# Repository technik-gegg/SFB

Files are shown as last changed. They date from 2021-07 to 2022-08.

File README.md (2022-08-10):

# Welcome to the SFB project

This is the firmware for the **S**mart **F**ilament **B**uffer as published on [Printables](https://www.printables.com/de/model/197621-smart-filament-buffer-2) and [Thangs](https://thangs.com/mythangs/file/58718).

The Smart Filament Buffer (used for multi-material 3D printing) comes with an integrated 5 fold filament run-out detector, which is based on the Arduino Nano and a bunch of linear Hall-Effect sensors.
An integrated I2C OLED makes reading the current status and it's configuration a breeze.

This project utilizes PlatformIO and VS-Code. Make sure you have those tools installed on your PC/Mac, open the project in VS-Code, build it, flash it onto the Arduino Nano and you're all set to go.

The schematic for this project is pretty simple and straight forward:

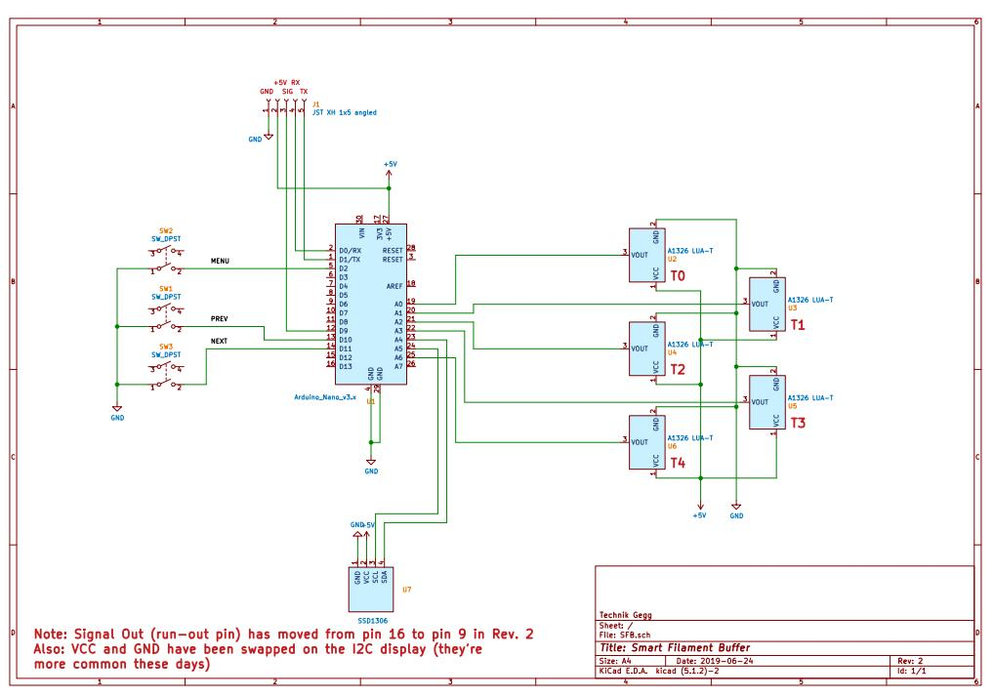
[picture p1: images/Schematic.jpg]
Schematic


All the electronics will fit onto a standard 60x40 mm prototype board.

If you don't feel like wiring all this up on a prototype board by hand, head over to my [PCB repository at AISLER](https://aisler.net/technik-gegg/smuff/sfb-pcb) where you can comfortably order one or more PCB(s) right away. Usually, you will get your PCB made and delivered within 7 (work) days.

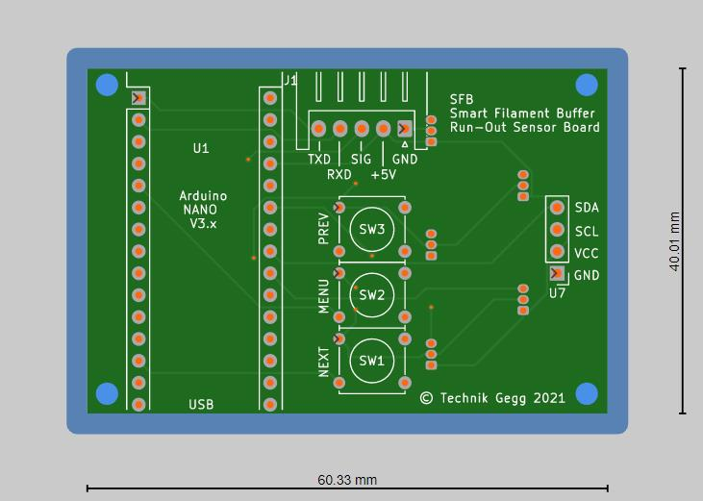
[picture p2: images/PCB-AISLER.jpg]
PCB-AISLER (https://aisler.net/technik-gegg/smuff/sfb-pcb)

<figure>
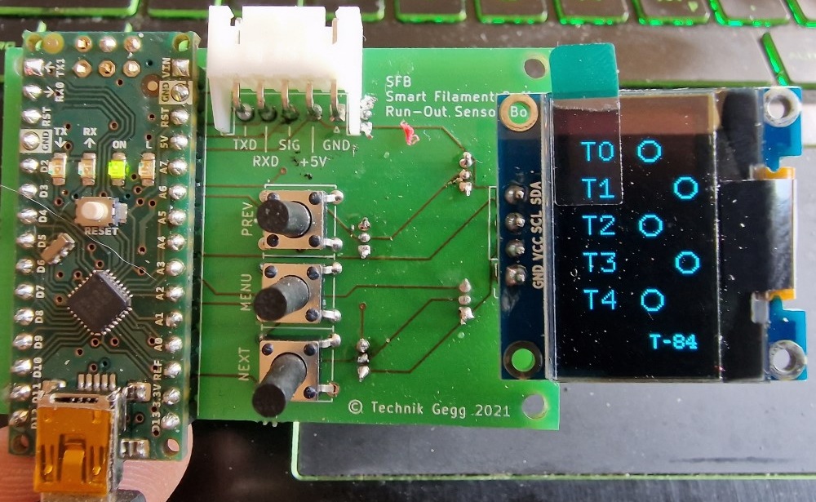
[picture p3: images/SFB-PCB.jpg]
Assembled SFB PCB
    
    <figcaption>Assembled PCB, with courtesy of maker Defenc</figcaption>
</figure>

Beside the Arduino Nano, the OLED and sensors, you have 3 push buttons, labelled *PREV*, *MENU* and *NEXT*, to handle the integrated menus.
Connector J1 is being used to attach the SFB to your 3D printer, which will supply the power to the SFB on pins 1 and 2 (GND/+5V).
Pin 3 (SIG) is used to connect the run-out signal to the E-STOP header on your 3D printer controller, which becomes HIGH (+5V) as soon as a run-out is triggered.

Configured correctly, this run-out signal will cause your 3D Printer to pause the print before it starts printing hot air.

On a Duet3D controller board for example, you'll need to add these two lines of GCode in your *config.g*:

```Gcode
M591 D0 P2 C2 S1        ; Set filament sensing sensor to switch (active high)
M581 E0 T1 S1 C1        ; Configure external trigger to pause the print only when printing
```

Klipper in contrast requires you to configure the according pin of the "runout_sensor" in your *printer.cfg* file, i.e. pin GPIO16, active high:

```Python
[filament_switch_sensor runout_sensor]
switch_pin: gpio16
pause_on_runout: True
```

In Marlin you'll need to enable and set up the run-out sensor in your *Configuration.h* file, compile and flash the new firmware. For example: Pin PA15, active high:

```Arduino
#define FILAMENT_RUNOUT_SENSOR
#if ENABLED(FILAMENT_RUNOUT_SENSOR)
  #define FIL_RUNOUT_ENABLED_DEFAULT true    // Enable the sensor on startup. Override with M412 followed by M500.
  #define NUM_RUNOUT_SENSORS   1             // Number of sensors, up to one per extruder. Define a FIL_RUNOUT#_PIN for each.
  
  #define FIL_RUNOUT1_PIN      PA15          // Depends on your controller board!
  #define FIL_RUNOUT1_STATE    HIGH          // Pin state indicating that filament is NOT present.
  #define FIL_RUNOUT1_PULLDOWN               // Use internal pulldown for filament runout pins.
  ...
#endif
```

Pin 4 (RX) and Pin 5 (TX) of J1 are routed to the Arduino Nano serial port, which can be used to command the SFB to monitor a specific tool only. If none is set (T= -1), all sensors are monitored and the run-out triggers as soon as no sensor reports detecting "filament loaded".
Ideally, this communication path is wired to your controller (either your 3D printer or the SMuFF) in order to set up the tool to monitor automatically during a print.

# Calibration

Before the SFB is ready to use, you'll need to calibrate it. Therefore, press the *MENU* button to open the main menu and select the item **Sensors**. The SFB will print the current sensor values on the display. Take care that, as long as no filaments are loaded, all sensors are within the same value range (+-20 Gs).
If one or more of the sensors show a negative value while all others show positive values, you have to flip the magnets - of those showing negatives - upside-down.
Once you push against the steel ball of one of the sensors, the sensor readout will raise towards the max. value of 640 (Gs). This way you're able to check whether all sensors are working correctly.
Once all sensors are in the same (lower) range, press the **PREV** button to start the calibration sampling. After the sampling is done, the SFB will show the min./max. Gauss values at the very bottom of the display.
Now press the **NEXT** button in order to store these values in EEPROM and the calibration is done.

# Run-out detection

In "simple mode", the run-out detection does not need to know which filament is currently in use. It will monitor all sensors continously and as soon as all of them are below the threshold (1.75 times the calibrated min. Gauss value), it'll start the run-out countdown after which the run-out is signaled.
If one of the sensors gets triggered while the countdown is running, the countdown will be interrupted and the counter reset. This behaviour is needed for retractions and/or tool changes.
Via the integrated menu **Trigger**, you're able to change the countdown timespan (15 to 120 seconds), which gets stored in the Arduinos EEPROM.

In "control mode" (means: your SFB is connected to either the SMuFFs or the 3D printers TTL serial interface via the *RX* pin), the SFB will monitor the run-out for the requested tool only, which is set after a **Tn** command has been received (n = tool number). All other sensors will be ignored and also not drawn onto the display.
This stays valid until the tool is being reset by a **T-1** command, which basically instructs the SFB to return to "simple mode". *Please notice: Once a tool has been set, it'll be stored in the EEPROM, so that the current tool will stay active even after the SFB has been reset*

# Daisy-Chaining SFBs

Daisy-Chaining SFB devices allows you to handle more than 5 tools/filaments (up to 20).
In order to use this feature, you need to add a wire from the **SIG** output of the next device to pin **TX** of the current device, set it to **Chained**/**Last** in the settings menu **Mode** and assign an ID in settings menu **Device** (according to the picture below). **Chained** means there is yet another device in the chain sending a run-out signal, **Last** means this is the very last device in the chain.

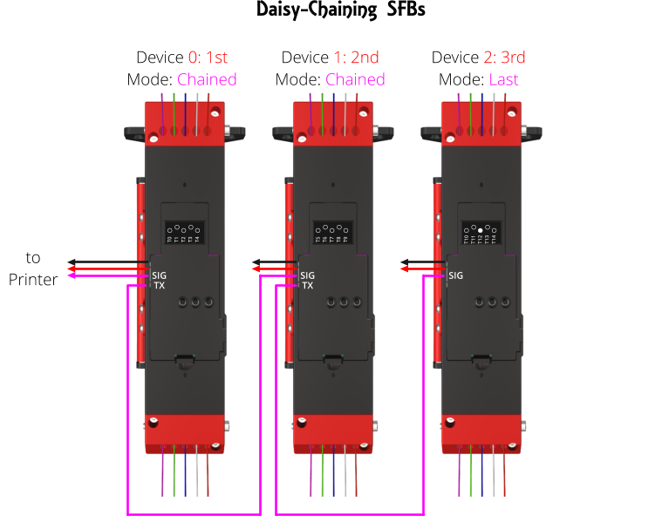
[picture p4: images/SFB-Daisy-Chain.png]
Daisy-Chain


In Daisy-Chain mode only the first (0: 1st) SFB will pass the run-out signal to the 3D Printer, which follows the same strategy as with one SFB in "normal" mode, whereas the "last" device will initiate the run-out countdown.
Also, numbering of the tools will be set according to the device IDs, i.e. T0-T4 on *1st*, T5-T9 on *2nd*, T10-T14 on *3rd*.

**Please keep in mind:**

+ In Daisy-Chain mode the *TX* pin of the SFB will be detached internally and thus, it won't be able to send any data back to the controller. Though, you're still able to send *Tn* commands from the controller to the device.
+ *For flashing the firmware you **must** detach the connector from J1.*
+ All devices need to be powered with +5V/GND from the same source.
+ In order to use the tool select feature (monitoring only one sensor) all devices must be able to receive the according command via the *RX* pin. This may require adding an external driver IC (i.e. [SN74LS126A](https://www.ti.com/lit/ds/symlink/sn74ls126a.pdf) or similar) between the *TX* wire of the senders serial interface and the *RX* input of the SFBs if you encounter the SFBs aren't reacting to the T*n* commands.

# Credits

A shout-out goes to [Oliver Kraus]( https://github.com/olikraus/U8G2_Arduino) for his amazing U8G2 display library and [Albert van Dalen](https://github.com/avandalen/avdweb_AnalogReadFast) for his fast analog library.

# Recent changes

### 2022-08-10

+ overhauled this README
+ added overflow prevention while setting the run-out timer.
+ added [Albert van Dalen's library](https://github.com/avandalen/avdweb_AnalogReadFast) for a faster read out of the Hall sensor values.
+ added option to show the *Info* screen when pressing the **PREV** button in main screen.
+ added option to show the *Sensors* screen when pressing the **NEXT** button in main screen.
+ added configurable rotation of the tool names (T*n*) on the main screen for better readability in different orientations of the SFB. Everything else stays in Portrait mode.
+ prefixed debug messages with "echo:" to not spam the 3D printer controller.

### 2022-08-08

+ status display on startup (reset) will show the current Mode and device ID.
+ renamed menu item *Defaults* to *\*Reset\** because it fits better and makes more sense actually.
+ added Daisy-Chain mode, which allows you to "chain up" multiple SFBs to one virutally bigger unit.

### 2022-08-06

+ replaced the Full buffer of the OLED display with Page buffers because the Arduino ran into low memory issues. Refresh/drawing of the display will be a bit slower now.
+ added sending some debug messages to the serial port while the device is initializing.

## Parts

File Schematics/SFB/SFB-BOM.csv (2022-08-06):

Source: | D:\Data\PlatformIO\SFB\SFB\Schematics\SFB\SFB.sch
Date: | 02.08.2021 18:03:10
Tool: | Eeschema (5.1.2)-2
Component Count: | 11
Ref | Value | Footprint | Datasheet | Manufacturer | Vendor
J1 | JST XH 1x5 angled | Connector_JST:JST_XH_S5B-XH-A_1x05_P2.50mm_Horizontal | ~
SW1 | SW_DPST | SFB:SW_Tactile_Straight_KSA0Axx1LFTR-4Pin | ~
SW2 | SW_DPST | SFB:SW_Tactile_Straight_KSA0Axx1LFTR-4Pin | ~
SW3 | SW_DPST | SFB:SW_Tactile_Straight_KSA0Axx1LFTR-4Pin | ~
U1 | Arduino_Nano_v3.x | Module:Arduino_Nano | http://www.mouser.com/pdfdocs/Gravitech_Arduino_Nano3_0.pdf
U2 | A1326 LUA-T | Package_TO_SOT_THT:TO-92Flat | http://www.allegromicro.com/~/media/Files/Datasheets/A1301-2-Datasheet.ashx
U3 | A1326 LUA-T | Package_TO_SOT_THT:TO-92Flat | http://www.allegromicro.com/~/media/Files/Datasheets/A1301-2-Datasheet.ashx
U4 | A1326 LUA-T | Package_TO_SOT_THT:TO-92Flat | http://www.allegromicro.com/~/media/Files/Datasheets/A1301-2-Datasheet.ashx
U5 | A1326 LUA-T | Package_TO_SOT_THT:TO-92Flat | http://www.allegromicro.com/~/media/Files/Datasheets/A1301-2-Datasheet.ashx
U6 | A1326 LUA-T | Package_TO_SOT_THT:TO-92Flat | http://www.allegromicro.com/~/media/Files/Datasheets/A1301-2-Datasheet.ashx
U7 | SSD1306 | Connector_PinHeader_2.54mm:PinHeader_1x04_P2.54mm_Vertical

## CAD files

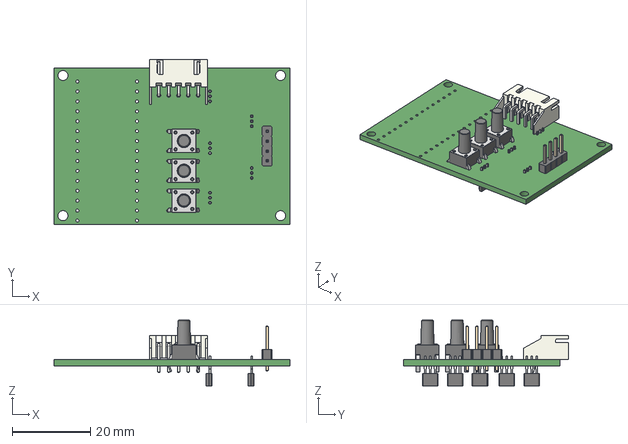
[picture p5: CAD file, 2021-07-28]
Schematics/SFB/SFB.step
60.3 x 42.2 x 16.8 mm

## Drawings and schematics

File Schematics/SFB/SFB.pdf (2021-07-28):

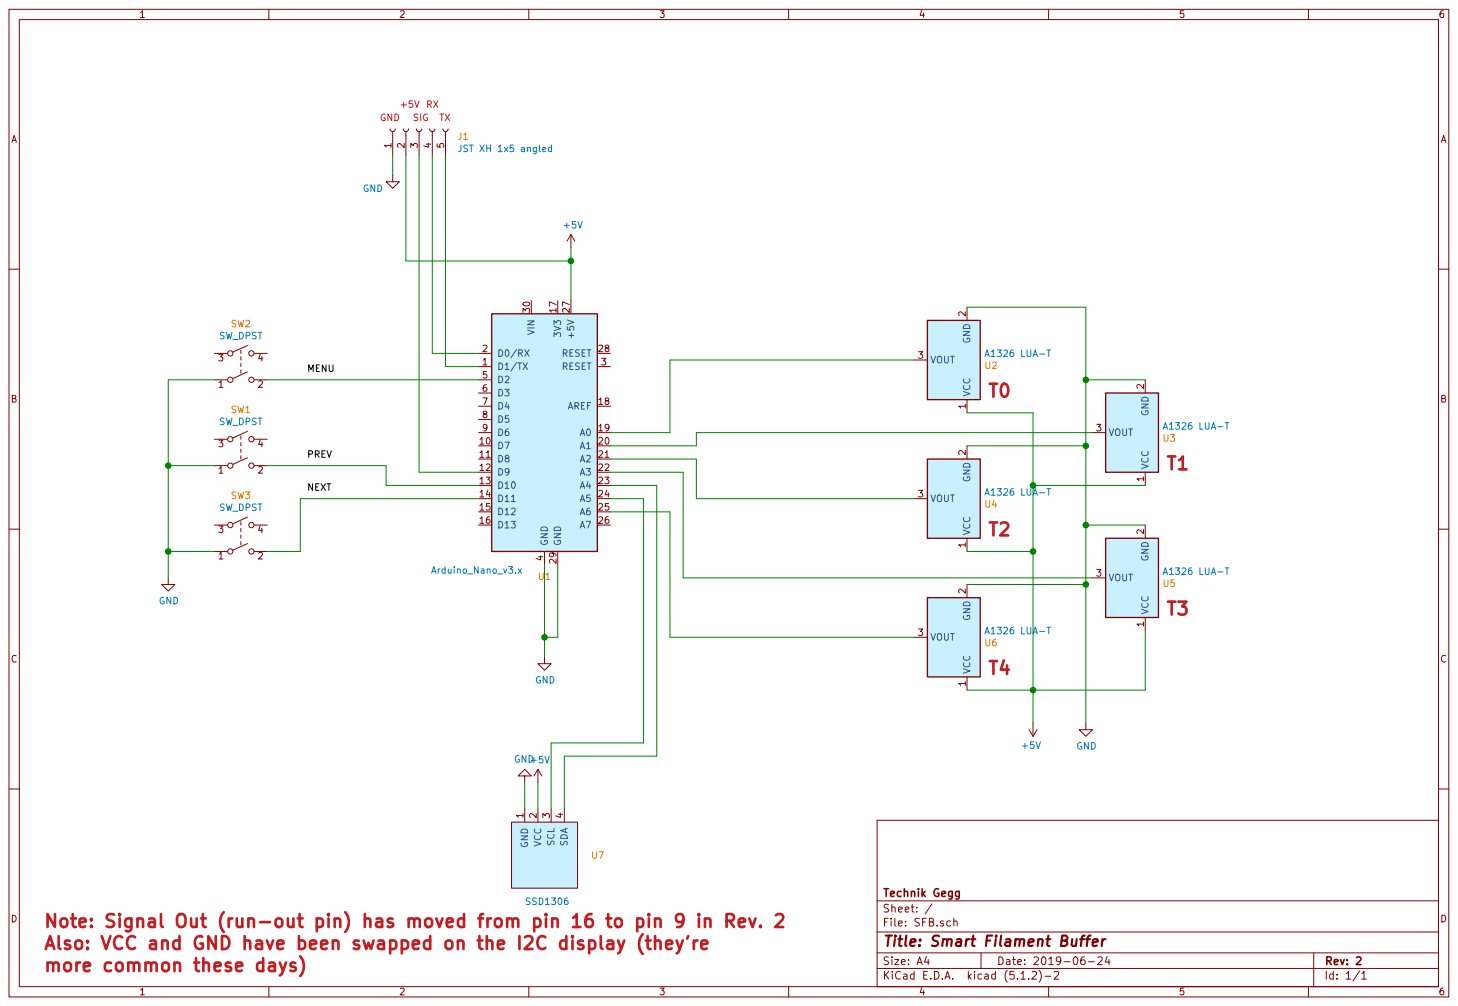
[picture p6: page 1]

JST XH 1x5 angled GNDGND

2 VOUT 3 U5A1326 LUA-T GND GND

4 U7 SSD1306 Note: Signal Out (run-out pin) has moved from pin 16 to pin 9 in Rev. 2

Id: 1/1 Title: Smart Filament Buffer File: SFB.sch Sheet: / Technik Gegg

Also: VCC and GND have been swapped on the I2C display (they're
more common these days)

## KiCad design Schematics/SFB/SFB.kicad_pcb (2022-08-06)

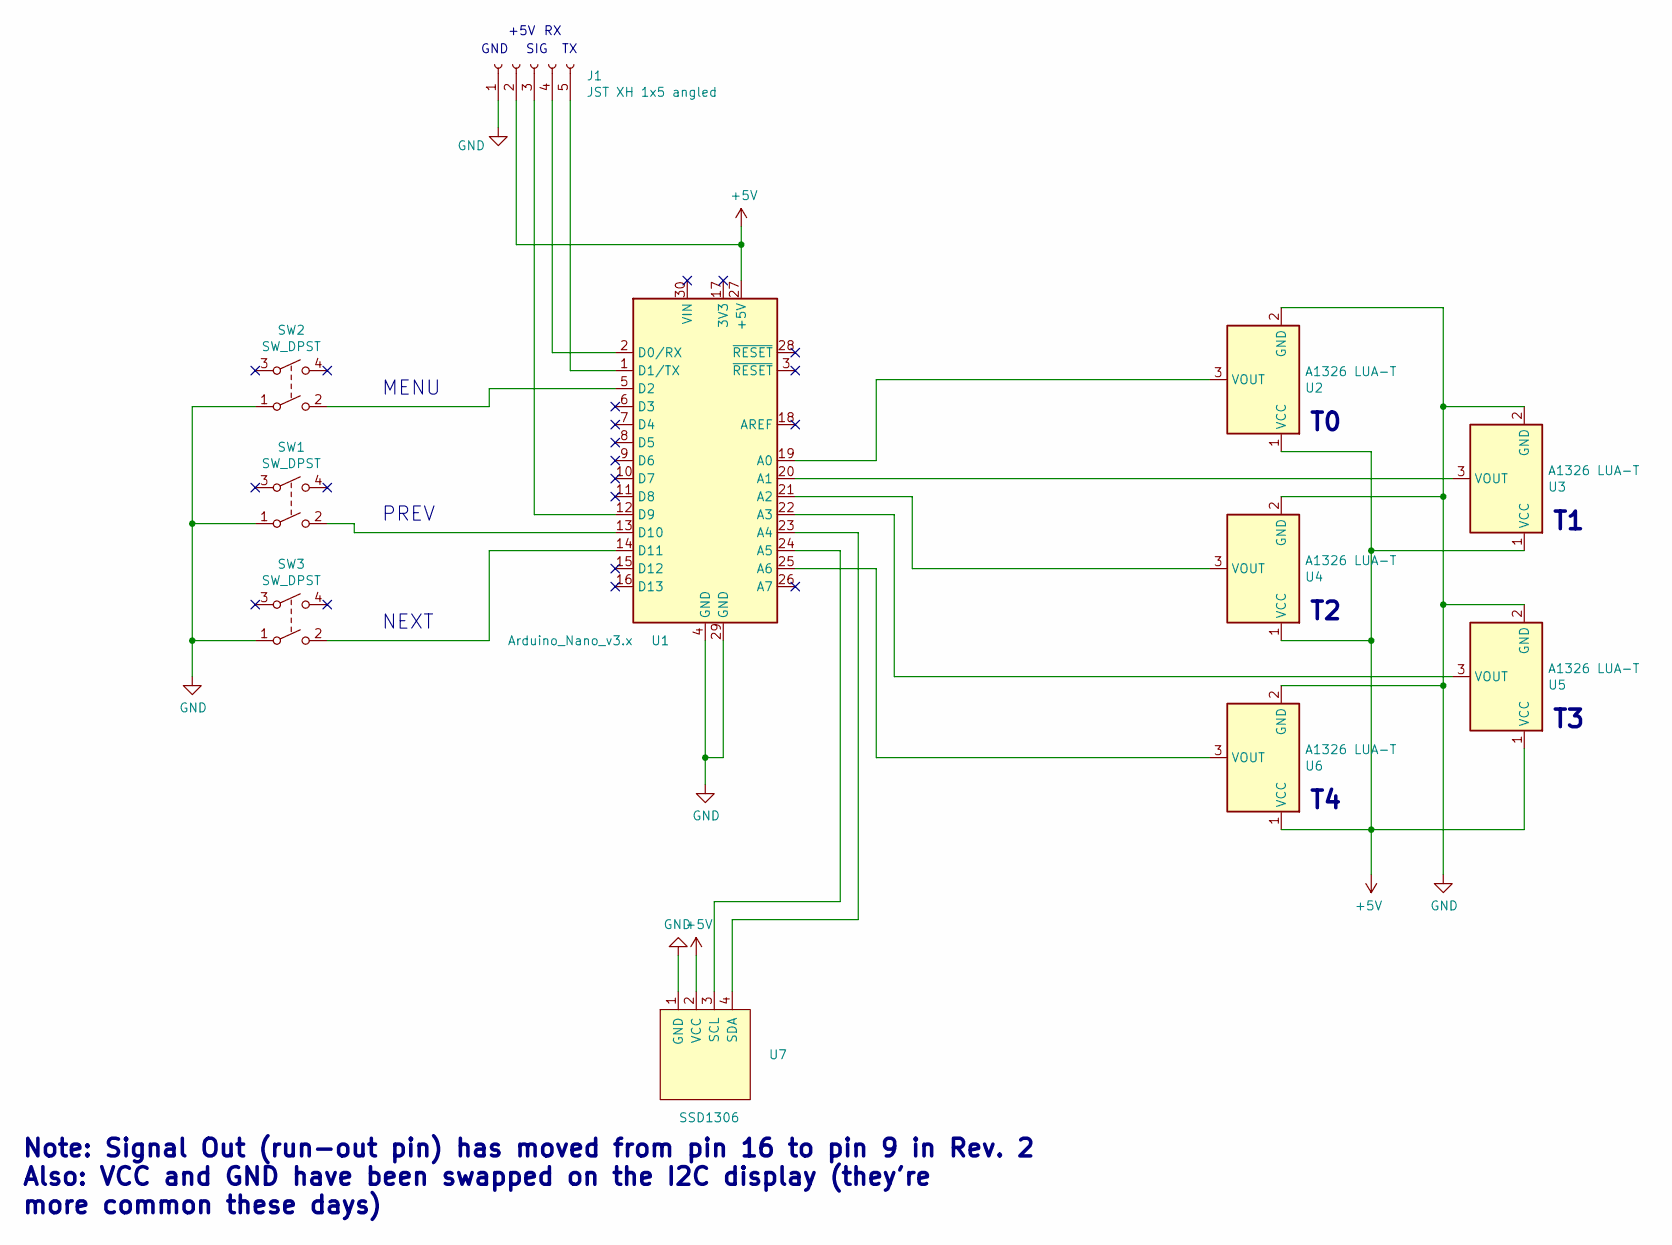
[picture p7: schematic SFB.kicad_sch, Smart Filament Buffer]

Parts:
J1: JST XH 1x5 angled; JST_XH_S5B-XH-A_1x05_P2.50mm_Horizontal
SW1, SW2, SW3: SW_DPST; SW_Tactile_Straight_KSA0Axx1LFTR-4Pin
U1: Arduino_Nano_v3.x; Arduino_Nano
U2, U3, U4, U5, U6: A1326 LUA-T; TO-92Flat
U7: SSD1306; PinHeader_1x04_P2.54mm_Vertical

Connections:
+5V: J1.2, U1.27 (+5V), U2.1 (VCC), U3.1 (VCC), U4.1 (VCC), U5.1 (VCC), U6.1 (VCC), U7.2 (VCC)
GND: J1.1, SW1.1, SW2.1, SW3.1, U1.4 (GND), U1.29 (GND), U2.2 (GND), U3.2 (GND), U4.2 (GND), U5.2 (GND), U6.2 (GND), U7.1 (GND)
unnamed: J1.3, U1.12 (D9)
unnamed: J1.4, U1.2 (D0/RX)
unnamed: J1.5, U1.1 (D1/TX)
unnamed: SW1.2, U1.13 (D10)
unnamed: SW2.2, U1.5 (D2)
unnamed: SW3.2, U1.14 (D11)
unnamed: U1.19 (A0), U2.3 (VOUT)
unnamed: U1.20 (A1), U3.3 (VOUT)
unnamed: U1.21 (A2), U4.3 (VOUT)
unnamed: U1.22 (A3), U5.3 (VOUT)
unnamed: U1.23 (A4), U7.4 (SDA)
unnamed: U1.24 (A5), U7.3 (SCL)
unnamed: U1.25 (A6), U6.3 (VOUT)

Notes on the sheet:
MENU
PREV
Note: Signal Out (run-out pin) has moved from pin 16 to pin 9 in Rev. 2 Also: VCC and GND have been swapped on the I2C display (they're more common these days)
GND
+5V
NEXT
SIG

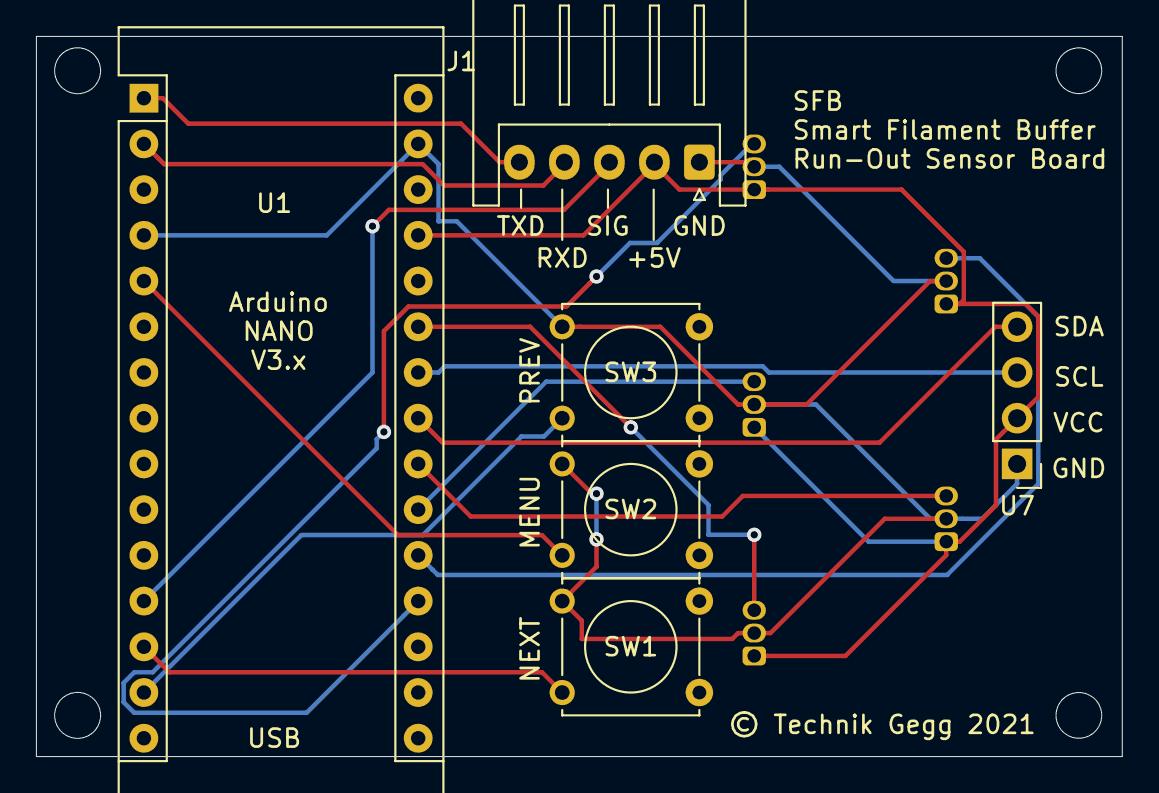
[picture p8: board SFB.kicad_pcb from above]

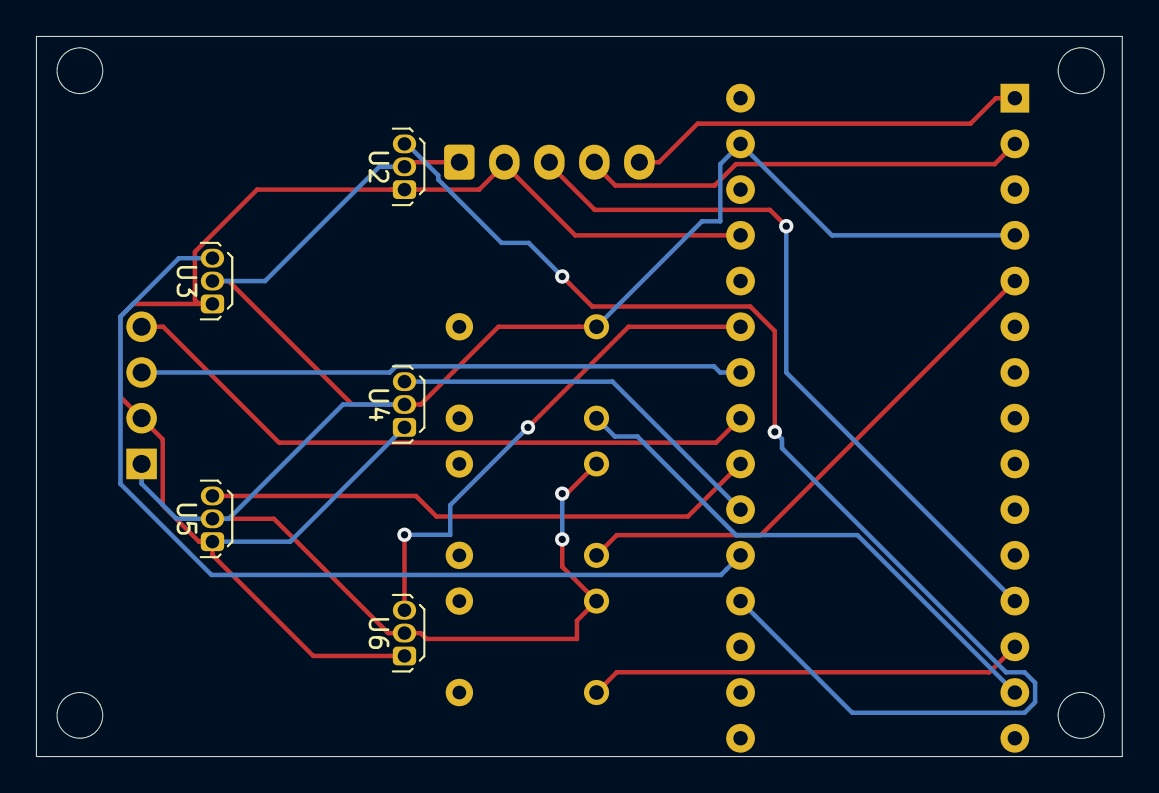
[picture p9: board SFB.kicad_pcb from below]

Board: 2 copper layers, 60.3 x 40.0 mm, 11 parts (5 on the bottom side), 15 nets.

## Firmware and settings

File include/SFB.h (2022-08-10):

/**
 * SFB Firmware
 * Copyright (C) 2019 Technik Gegg
 *
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
 */

#pragma once

#include <Arduino.h>
#include <U8g2lib.h>


#define EEP_TRIGGER_ADR 1
#define EEP_SENSMIN_ADR 2
#define EEP_SENSMAX_ADR 4
#define EEP_DEVICE_ADR  6
#define EEP_DEVMODE_ADR 8
#define EEP_DEVLAST_ADR 10
#define EEP_TOOL_ADR    12
#define EEP_ROTATE_ADR  14

#define SERIAL_BAUDRATE 115200      // Baudrate for serial communication

#define MAX_SENSOR      5           // the number of Hall-sensors
#define MAX_TOOLS       20          // the max. number of tools supported
#define MAX_SAMPLES     150         // number of samples for calibration
#define MIN_GAUSS       -640        // min. Gauss value the Hall sensor reads
#define MAX_GAUSS       640         // max. Gauss value the Hall sensor reads

#if defined(ARDUINO_PRO_MICRO)
#define TRIGGER_PIN     6           // output pin for triggering filament runout
#define TRIGGERIN_PIN   1           // input pin for triggering filament runout (for daisy-chaining)
#define NEXT_PIN        8           // NEXT button pin
#define MENU_PIN        7           // MENU button pin
#define PREV_PIN        9           // PREV button pin 
#define LED_PIN         0           // no built-in LED
#else
#define TRIGGER_PIN     9           // output pin for triggering filament runout (changed from 13 in previous version)
#define TRIGGERIN_PIN   1           // input pin for triggering filament runout (for daisy-chaining)
#define NEXT_PIN        11          // NEXT button pin
#define MENU_PIN        2           // MENU button pin
#define PREV_PIN        10          // PREV button pin 
#define LED_PIN         LED_BUILTIN // built-in LED pin
#endif

#define LOOP_DELAY      10          // delay for loop()
#define SCREEN_TIMEOUT  60*3        // turn screen off after 3 minutes to avoid OLED burn-in
#define MENU_TIMEOUT    10000
#define SENSORS_TIMEOUT 30000       // leave Sensors screen after this idle timeout
#define INFO_TIMEOUT    7           // timeout for settings summary after startup (in seconds)
#define PRESCALER       256
#define SECOND_COUNTER  65536 - (F_CPU/PRESCALER) // usually 3036
#define DEFAULT_TRIGGER 120
#define DEFAULT_SENSMIN 50
#define DEFAULT_SENSMAX 500
#define MAX_SECONDS     3600

#define ArraySize(arr) (sizeof(arr) / sizeof(arr[0]))

void    showTriggerMenu();
void    showSensors();
void    showDeviceMenu();
void    showModeMenu();
void    showRotateTools();
void    setDefaults();
bool    setChained();
void    setupTimer();
void    signalRunout(bool);
void    draw();
void    drawSamplingStat(char*);
void    menuInterrupt();
void    readSensors();
void    reboot();
void    setFontBig();
void    setFontSmall();
void    showParams();
int     getAnalogValue(uint8_t port);
uint8_t scanI2C();
void    resetScreenSaver();
void    debounceButtons();
void    __log(const char *fmt, ...);

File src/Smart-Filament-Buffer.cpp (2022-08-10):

/**
 * SFB Firmware
 * Copyright (C) 2019-2022 Technik Gegg
 *
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
 */

/*
 Uncomment the  following line to compile for a Arduino PRO MICRO (LEONARDO).

 Be aware, that platformIO has issues with programming such devices!
 Hence, you have to copy the source file as "Smart-Filament-Buffer.ino" into an
 separate folder named "Smart-Filament-Buffer", copy the SFB.h into it as well
 and compile and upload this firmware using the Arduino IDE!
*/
//#define ARDUINO_PRO_MICRO 1   

#include "SFB.h"
#include <EEPROM.h>
#include <Wire.h>
#include "avdweb_AnalogReadFast.h"

U8G2_SSD1306_128X64_NONAME_2_HW_I2C display(U8G2_R1, /* reset=*/ U8X8_PIN_NONE);


bool          runout[MAX_SENSOR];       // state storage for run-out detection
int           runoutTime;               // timer value for latest run-out detected
uint8_t       sensorsIn[MAX_SENSOR] = { 
                  A0, A1, A2, A3, A6    // sensor inputs for T0..T4
              };
byte          runoutTrigger;            // time in seconds to trigger run-out on the controller board
int           gaussMin;                 // Gauss values min./max. for "filament run-out" detection
int           gaussMax;
int           screenSaver;              // counter for screen saver
volatile bool isPowerSave;              // screen saver ON flag 
bool          showMenu;                 // show menu flag
bool          lastTriggerState;         // last filament state
bool          isInit = true;            // flag for displaying params at start
int           seconds;                  // seconds counter
int8_t        tool = -1;                // current tool to monitor (-1 means all tools)
int8_t        device = 0;               // current device for daisy-chain
int8_t        lastDevice = 0;           // 1 for last device in a daisy-chain
int8_t        deviceMode = 0;           // device mode (0=standalone, 1=daisy-chain)
bool          deviceRunout = false;     // set if the local device has triggered runout in Daisy-Chain mode
bool          triggerIn = false;        // input trigger coming from next device
bool          txDisabled = false;       // set if TX is being disabled (sending text isn't possible anymore)
int           infoTimeout = 0;          // time to hide info screen
int8_t        rotateTools = 0;          // rotate tools on main display 0=normal, 1=90 deg, 3=270 deg.

void setFontBig() {
  display.setFont(u8g2_font_9x15_tf);   // set default font
}

void setFontSmall() {
  display.setFont(u8g2_font_profont11_tr);  // set smaller font
}

void resetScreenSaver() {
  screenSaver = seconds;
  isPowerSave = false;
}

int getAnalogValue(uint8_t port) {
  int val = (analogReadFast(port) & 0x3F8);       // map out lower 3 bits of the analog value
  long gauss = map(val, 0, 1023, MIN_GAUSS, MAX_GAUSS);  // convert analog value to Gaussian value
  return (int)gauss;
}

/* 
  Scans the I2C bus. 
  At least one device is supposed to be found, the OLED at 0x3C.
*/
uint8_t scanI2C() {
  uint8_t cnt = 0;
  Wire.begin();
  for (uint8_t address = 1; address < 127; address++)
  {
    Wire.beginTransmission(address);
    if (Wire.endTransmission() == 0) {
      __log(PSTR("I2C device found at address 0x%x"), address);
    }
    delay(3);
  }
  return cnt;
}

void showMainMenu() {

  bool      stopMenu = false;
  bool      isChained = deviceMode != 0;
  unsigned  startTime = millis();
  uint8_t   current_selection = 0;
  char      caption[40];
  char      buf[60];
  
  setFontBig();
  sprintf_P(caption, PSTR("Options"));

  do {
    // debounce Menu input
    while(digitalRead(MENU_PIN) == LOW) {
      yield();
    }
    
    snprintf_P(buf, ArraySize(buf), PSTR("Trigger\nSensors\nMode\nDevice\nRotate\n---\n*Reset*\n---\nEXIT"));
    current_selection = display.userInterfaceSelectionList(caption, current_selection, buf);

    if(current_selection == 0)
      return;

    else {
      switch(current_selection) {
        case 1:
          showTriggerMenu();
          startTime = millis();
          break;
        
        case 2:
          showSensors();
          startTime = millis();
          break;

        case 3:
          showModeMenu();
          startTime = millis();
          break;

        case 4:
          if(deviceMode == 0)
            isChained = setChained();
          if(isChained)
            showDeviceMenu();
          startTime = millis();
          break;

        case 5:
          showRotateTools();
          startTime = millis();
          break;
        
        case 6:
        case 8:
          startTime = millis();
          break;

        case 7:
          setDefaults();
          startTime = millis();
          break;

        case 9:
          stopMenu = true;
          break;
      }
    }
    if(millis()-startTime > MENU_TIMEOUT) {
      stopMenu = true;
    }
  } while(!stopMenu);
  showMenu = false;
  resetScreenSaver();
}

/*
  Shows the raw values of each sensor.
  Menu button leaves this mode.
  Next button starts sampling for the highest value (gaussMin), which is used as run-out trigger value.
  Prev button stores the gaussMin in EEPROM.
*/
void showSensors() {
  setFontBig();
  display.setFontPosTop();

  bool stopMenu = false;
  bool isSampling = false;
  bool isStored = false;
  int x, y, samples = 0;
  int maxGauss;
  int minGauss;
  char buf[25];
  int  hallValues[MAX_SENSOR];
  
  debounceButtons();
  unsigned long start = millis();

  do {
    if(digitalRead(NEXT_PIN) == LOW && !isSampling) {
      isSampling = true;
      isStored = false;
      samples = 0;
      minGauss = MIN_GAUSS;
      maxGauss = MAX_GAUSS;
      start = millis();
    }
    if(digitalRead(PREV_PIN) == LOW && !isSampling) {
      EEPROM.put(EEP_SENSMIN_ADR, minGauss);
      EEPROM.put(EEP_SENSMAX_ADR, maxGauss);
      gaussMin = minGauss;
      gaussMax = maxGauss;
      isStored = true;
      samples = 0;
      start = millis();
    }
    for(int8_t i=0; i< MAX_SENSOR; i++) {
      int gauss = getAnalogValue(sensorsIn[i]);
      if(isSampling) {
        if(samples < MAX_SAMPLES) {
          if(abs(gauss) > minGauss)
            minGauss = (int)((float)(abs(gauss)/10+1) * 10);
        }
      }
      hallValues[i] = gauss;
    }
    display.firstPage();
    do {
      for(int8_t i=0; i< MAX_SENSOR; i++) {
        int gauss = hallValues[i];
        y = i*21+12; x = 5;
        sprintf_P(buf,PSTR("T%d"), i+(device*MAX_SENSOR));
        display.drawStr(x, y, buf);
        sprintf_P(buf, PSTR("%4d"), gauss);
        display.drawStr(x+22, y, buf);
      }
      if(isSampling) {
        if(samples < MAX_SAMPLES)
          sprintf_P(buf,PSTR("SAMPLE MIN"));
        drawSamplingStat(buf);
        samples++;
      }
      else if(isStored) {
        sprintf_P(buf, PSTR("STORED!"));
        drawSamplingStat(buf);
      }

      if(samples >= MAX_SAMPLES) {
        if(minGauss > 0) {
          sprintf_P(buf,PSTR("%3d/%3d"), minGauss, maxGauss);
          drawSamplingStat(buf);
        }
        isSampling = false;
      }
    } while (display.nextPage());
    
    if(digitalRead(MENU_PIN) == LOW)
      stopMenu = true;
    if(millis()-start >= SENSORS_TIMEOUT)
      stopMenu = true;
  } while(!stopMenu);
  resetScreenSaver();
}

void showTriggerMenu() {

  char caption[20];
  char buf[50];
  sprintf_P(caption, PSTR("Trigger"));
  uint8_t current_selection;
  bool stopMenu = false;

  switch(runoutTrigger) {
    case 15:  current_selection = 1; break;
    case 30:  current_selection = 2; break;
    case 45:  current_selection = 3; break;
    case 60:  current_selection = 4; break;
    case 90:  current_selection = 5; break;
    case 120: current_selection = 6; break;
    default:  current_selection = 0; break; 
  }
  do {
    setFontBig();
    snprintf_P(buf, ArraySize(buf), PSTR("15s\n30s\n45s\n60s\n90s\n120s\n---\nEXIT"));
    current_selection = display.userInterfaceSelectionList(caption, current_selection, buf);

    switch(current_selection) {
      case 1:
        runoutTrigger = 15;
        break;
      
      case 2:
        runoutTrigger = 30;
        break;

      case 3:
        runoutTrigger = 45;
        break;

      case 4:
        runoutTrigger = 60;
        break;

      case 5:
        runoutTrigger = 90;
        break;

      case 6:
        runoutTrigger = 120;
        break;
      
      default:
        stopMenu = true;
        break;
    }
    if(current_selection >= 1 && current_selection <=6) {
      EEPROM.update(EEP_TRIGGER_ADR, runoutTrigger);
      stopMenu = true;
    }
  } while(!stopMenu);
}

void showDeviceMenu() {

  char caption[20];
  char buf[50];
  sprintf_P(caption, PSTR("Device"));
  uint8_t current_selection = 0;
  bool stopMenu = false;

  if(device >=0 && device <= 3)
    current_selection = device + 1;

  do {
    setFontBig();
    snprintf_P(buf, ArraySize(buf), PSTR("0: 1st\n1: 2nd\n2: 3rd\n3: 4th\n---\nEXIT"));
    current_selection = display.userInterfaceSelectionList(caption, current_selection, buf);

    switch(current_selection) {
      case 1:
        device = 0;
        break;
      
      case 2:
        device = 1;
        break;

      case 3:
        device = 2;
        break;

      case 4:
        device = 3;
        break;

      default:
        stopMenu = true;
        break;
    }
    if(current_selection >= 1 && current_selection <= 4) {
      EEPROM.update(EEP_DEVICE_ADR, device);
      stopMenu = true;
    }
  } while(!stopMenu);
}

void showModeMenu() {

  char caption[20];
  char buf[50];
  sprintf_P(caption, PSTR("Mode"));
  uint8_t current_selection = 0;
  bool stopMenu = false;

  if(deviceMode >=0 && deviceMode <= 1)
    current_selection = deviceMode + 1;
  if(lastDevice)
    current_selection = 3;

  do {
    setFontBig();
    snprintf_P(buf, ArraySize(buf), PSTR("Normal\nChained\nLast\n---\nEXIT"));
    current_selection = display.userInterfaceSelectionList(caption, current_selection, buf);

    switch(current_selection) {
      case 1:
        deviceMode = 0;
        lastDevice = 0;
        break;
      
      case 2:
        deviceMode = 1;
        lastDevice = 0;
        break;

      case 3:
        deviceMode = 1;
        lastDevice = 1;
        break;

      default:
        stopMenu = true;
        break;
    }
    if(current_selection >= 1 && current_selection <= 3) {
      EEPROM.update(EEP_DEVMODE_ADR, deviceMode);
      EEPROM.update(EEP_DEVLAST_ADR, lastDevice);
      stopMenu = true;
    }
  } while(!stopMenu);
  if(deviceMode == 0) {
    device = 0;
    lastDevice = 0;
    EEPROM.update(EEP_DEVICE_ADR, device);
    EEPROM.update(EEP_DEVLAST_ADR, lastDevice);
  }
}

void showRotateTools() {

  char caption[20];
  char buf[50];
  sprintf_P(caption, PSTR("Rotate"));
  uint8_t current_selection = 0;
  bool stopMenu = false;

  switch(rotateTools) {
    case 0:
      current_selection = 1;
      break;
    case 1:
      current_selection = 2;
      break;
    case 3:
      current_selection = 3;
      break;
  }

  do {
    setFontBig();
    snprintf_P(buf, ArraySize(buf), PSTR("0\u00b0\n90\u00b0\n270\u00b0\n---\nEXIT"));
    current_selection = display.userInterfaceSelectionList(caption, current_selection, buf);

    switch(current_selection) {
      case 1:
        rotateTools = 0;
        break;
      
      case 2:
        rotateTools = 1;
        break;

      case 3:
        rotateTools = 3;
        break;

      default:
        stopMenu = true;
        break;
    }
    if(current_selection >= 1 && current_selection <= 3) {
      EEPROM.update(EEP_ROTATE_ADR, rotateTools);
      stopMenu = true;
    }
  } while(!stopMenu);
}


void reboot() {
  display.clearDisplay();
  delay(500);
  asm volatile ("jmp 0");
}

void drawSamplingStat(char* buf) {
  setFontSmall();
  int y = display.getDisplayHeight()-10;
  display.setDrawColor(0);
  display.drawBox(0, y-2, display.getDisplayWidth(), display.getDisplayHeight()-y-1);
  display.setDrawColor(1);
  int x = display.getDisplayWidth() - display.getStrWidth(buf) - 2;
  display.drawStr(x, y, buf);
  setFontBig();
}

void showParams() {
  int x, y, h, w;
  char buf[30];
  // this can be interrupted by either Next or Prev buttons
  if(digitalRead(PREV_PIN) == LOW || digitalRead(NEXT_PIN) == LOW) {
    isInit = false;
    return;
  }
  y = 2; x = 2; 
  h = display.getMaxCharHeight()+5, w = display.getDisplayWidth();
  setFontSmall();
  display.setFontMode(1);
  display.drawBox(0, 0, w, h-2);
  display.setDrawColor(2);
  display.drawStr(x, y, "*Smart-FB*");                    y += h+2;
  display.setFontMode(0);
  display.setDrawColor(1);
  x = 0;
  display.drawStr(x, y, "Timeout");                       y += h;
  sprintf_P (buf, PSTR("[T%d] %d s"), tool, runoutTrigger);
  x = w-display.getStrWidth(buf)-2;
  display.drawStr(x, y, buf);                             y += h;
  x = 0;
  display.drawHLine(x, y-4, w);

  display.drawStr(x, y, "Mode/Dev.");                     y += h;
  if(deviceMode == 0)
    sprintf_P (buf, PSTR("%10s"), "Normal");
  else {
    sprintf_P (buf, PSTR("%6s: %1d%c"), "Chain", device, lastDevice>0 ? 'L' : '+');
  }
  x = w-display.getStrWidth(buf)-2;
  display.drawStr(x, y, buf);                             y += h;
  x = 0;
  display.drawHLine(x, y-4, w);

  display.drawStr(x, y, "Sensor");                    y += h;
  sprintf_P (buf, PSTR("min %3d Gs"), gaussMin);
  x = w-display.getStrWidth(buf)-2;
  display.drawStr(x, y, buf);                             y += h-4;
  sprintf_P (buf, PSTR("max %3d Gs"), gaussMax);
  x = w-display.getStrWidth(buf)-2;
  display.drawStr(x, y, buf);
}


void draw() {

  int x, y;
  char buf[30];

  display.setFontPosTop();
  // show parameters set in EEPROM after startup for a couple seconds
  if(seconds < infoTimeout && isInit) {
    showParams();
    return;
  }
  else {
    isInit = false;
  }
  setFontBig();

  for(int8_t i=0; i< MAX_SENSOR; i++) {
    y = i*21+10; x = 5;
    display.setFontDirection(rotateTools);
    if(rotateTools == 1) {
      x =  (i % 2 == 0) ? 14 : 27;
      y -= 4;
    }
    else if(rotateTools == 3) {
      x =  (i % 2 == 0) ? 7 : 20;
      y += 15;
    }
    // draw tool number
    sprintf_P(buf, PSTR("T%d"), i+(device*MAX_SENSOR));
    display.drawStr(x,y, buf);
    display.setFontDirection(0);
    // draw status of filament presence
    x = (i % 2 == 0) ? 45 : 58;
    y = i*21+16;
    if(tool == -1 || tool == i+(device*MAX_SENSOR)) {
      if(!runout[i])
        display.drawDisc(x, y, 5, U8G2_DRAW_ALL);
      else
        display.drawCircle(x, y, 5, U8G2_DRAW_ALL);
    }
    else {
      // not the currently monitored tool, then don't show status of this sensor at all
      display.setDrawColor(0);
      display.drawBox(x, y, 10, 10);
      display.setDrawColor(1);
    }
  }
  y += 13;
  // draw run-out if detected
  setFontSmall();
  if(runoutTime > 0) {
    if(runoutTrigger - (seconds - runoutTime) <= 0)
      sprintf_P(buf, PSTR("RUNOUT"));
    else
      sprintf_P(buf, PSTR("Rt-%d"), runoutTrigger - (seconds - runoutTime));
  }
  else {
    sprintf_P(buf, PSTR(" "));
    if(deviceMode != 0 && deviceRunout) {
      if(!triggerIn) {
        sprintf_P(buf, PSTR("*CHAINED*"));
      }
    }
    display.setDrawColor(0);
    display.drawBox(0, y-1, display.getDisplayWidth(), display.getDisplayHeight()-y-1);
    display.setDrawColor(1);
  }
  x = display.getDisplayWidth() - display.getStrWidth(buf) -2;
  display.drawStr(x, y, buf);
  setFontBig();

  if(deviceMode != 0 && lastDevice == 0) {
      // draw status of the (next) chained device
      if(triggerIn) {
        display.drawBox(0, y+1, 6, 6);
      }
      else {
        display.drawFrame(0, y+1, 6, 6);
      }
  }
}

void readSensors() {
  
  for(int8_t i=0; i< MAX_SENSOR; i++) {
    runout[i] = true;
    int gauss = getAnalogValue(sensorsIn[i]);
    if(gauss >= (gaussMin * 1.75)) {
      runout[i] = false;
    }
  }
  
  int runoutCnt = 0;
  if(tool == -1) {
    for(int8_t i=0; i< MAX_SENSOR; i++) {
      if(runout[i] == true) {
          runoutCnt++;
      }
    }
  }
  else {
    // monitoring only one sensor, check only that one
    if(runout[tool])
      runoutCnt = MAX_SENSOR;
  }
  triggerIn = digitalRead(TRIGGERIN_PIN) == HIGH;

  // check if a runout has to be signalled
  if(runoutCnt == MAX_SENSOR) {
    // in Daiys-Chain mode check the other devices as well
    if(deviceMode != 0 && lastDevice == 0) {
      deviceRunout = true;
      runoutTime = 0;
      if(!triggerIn) {
        signalRunout(false);
        return;
      }
      else {
        // runout signal from next device in chain is set
        // don't start a countdown, signal runout right away
        runoutTime = seconds - runoutTrigger;
        signalRunout(true);
        return;
      }
    }
    if(runoutTime == 0) {
      if(seconds + runoutTrigger >= MAX_SECONDS) {
        // prevent an overflow
        noInterrupts();
        seconds = 0;
        interrupts();
      }
      runoutTime = seconds;
    }
    if(seconds - runoutTime >= runoutTrigger) {
      signalRunout(true);
    }
  }
  else {
    signalRunout(false);
    deviceRunout = false;
    runoutTime = 0;
  }
}

void signalRunout(bool state) {
  if(state == lastTriggerState)
    return;
  if(state) {
    if(LED_PIN != 0)
      digitalWrite(LED_PIN, HIGH);      // turn built-in LED on on runout
    digitalWrite(TRIGGER_PIN, HIGH);
    isPowerSave = false;
  }
  else {
    if(LED_PIN != 0)
      digitalWrite(LED_PIN, LOW);
    digitalWrite(TRIGGER_PIN, LOW);
  }
  lastTriggerState = state;
}

void setDefaults() {
  char t1[10], t2[10], t3[10], btn[15];
  sprintf_P(t1,PSTR("Reset to"));
  sprintf_P(t2,PSTR("DEFAULTS"));
  sprintf_P(t3,PSTR("Sure?"));
  sprintf_P(btn,PSTR(" Yes \n NO "));
  setFontSmall();
  display.clearDisplay();

  if(display.userInterfaceMessage(t1, t2, t3, btn)!=1) {
    setFontBig();
    return;
  }
  runoutTrigger = DEFAULT_TRIGGER;
  gaussMin = DEFAULT_SENSMIN;
  gaussMax = DEFAULT_SENSMAX;
  EEPROM.put(EEP_TRIGGER_ADR, runoutTrigger);
  EEPROM.put(EEP_SENSMIN_ADR, gaussMin);
  EEPROM.put(EEP_SENSMAX_ADR, gaussMax);
  EEPROM.put(EEP_DEVICE_ADR, 0);
  EEPROM.put(EEP_DEVMODE_ADR, 0);
  EEPROM.put(EEP_DEVLAST_ADR, 0);
  EEPROM.put(EEP_TOOL_ADR, -1);
  EEPROM.put(EEP_ROTATE_ADR, 0);
  reboot();
}

bool setChained() {
  char t1[10], t2[10], t3[10], btn[15];
  sprintf_P(t1,PSTR("Set to"));
  sprintf_P(t2,PSTR("CHAINED"));
  sprintf_P(t3,PSTR("Sure?"));
  sprintf_P(btn,PSTR(" Yes \n NO "));
  setFontSmall();
  display.clearDisplay();

  if(display.userInterfaceMessage(t1, t2, t3, btn)!=1) {
    setFontBig();
    return false;
  }
  setFontBig();
  deviceMode = 1;
  EEPROM.put(EEP_DEVMODE_ADR, 1);
  return true;
}

void setupTimer() {
  noInterrupts();
  TCCR1A = 0;
  TCCR1B = 0;

  TCNT1 = SECOND_COUNTER;
  TCCR1B |= (1 << CS12);    // prescaler 256
  TIMSK1 |= (1 << TOIE1);
  interrupts();
}

ISR(TIMER1_OVF_vect)
{
  if(seconds < MAX_SECONDS)
    seconds++;
  else
    seconds = 0;
  TCNT1 = SECOND_COUNTER;
}

void menuInterrupt() {
  showMenu = false;
  if(isPowerSave) {
    resetScreenSaver();
    return;
  }
  if(seconds - screenSaver >= 1 && !isInit)
    showMenu = true;
}

void handleSerial(String& in) {
  // __log(PSTR("[IN]\t %s"), in.c_str());
  
  bool isQuery  = (in.length() >= 2 && in.charAt(1) == '?');

  switch(in.charAt(0)) {
    case 'T':       // either set or query active tool
      if(!isQuery) {
        long t = in.substring(1).toInt();
        if(t >= -1 && t < MAX_TOOLS) {
          tool = (int8_t)t;
          EEPROM.put(EEP_TOOL_ADR, tool);
        }
      }
      __log(PSTR("T%d"), tool);
      break;

    case 'N':       // either set or query Gauss Min value
      if(isQuery) {
        __log(PSTR("Gauss Min.: %d"), gaussMin);
      }  
      else {
        long g = in.substring(1).toInt();
        if(g >= DEFAULT_SENSMIN)
          gaussMin = (int)g;
        EEPROM.put(EEP_SENSMIN_ADR, gaussMin);
      }
      break;
    case 'X':       // either set or query Gauss Max value
      if(isQuery) {
        __log(PSTR("Gauss Max.: %d"), gaussMax);
      }  
      else {
        long g = in.substring(1).toInt();
        if(g < DEFAULT_SENSMAX)
          gaussMax = (int)g;
        EEPROM.put(EEP_SENSMAX_ADR, gaussMax);
      }
      break;
    case 'R':       // either set or query tool rotation
      if(isQuery) {
        __log(PSTR("Rotate tools.: %d deg."), rotateTools*90);
      }  
      else {
        long r = in.substring(1).toInt();
        switch(r) {
          case 0: rotateTools = 0; break;
          case 90: rotateTools = 1; break;
          case 270: rotateTools = 3; break;
          default: rotateTools = 0;
        }
        EEPROM.put(EEP_ROTATE_ADR, rotateTools);
      }
      break;
  }
}
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
void loop() {

  if(Serial.available()) {
    serialEvent();
  }
  if(showMenu) {
    if(!isInit)
      showMainMenu();
    else
      showMenu = false;
  }
  else {
    if(digitalRead(PREV_PIN) == LOW && !isInit) {
      isInit = true;
      isPowerSave = false;
      display.setPowerSave(0);
      infoTimeout = seconds + INFO_TIMEOUT;
      debounceButtons();
    }
    if(digitalRead(NEXT_PIN) == LOW && !isInit) {
      isPowerSave = false;
      display.setPowerSave(0);
      debounceButtons();
      showSensors();
    }

    display.setPowerSave(isPowerSave ? 1 : 0);
    readSensors();
    if(!isPowerSave) {
      display.firstPage();
      do {
        draw();
      } while(display.nextPage());
    }
  }
  delay(LOOP_DELAY);
  if(seconds - screenSaver >= SCREEN_TIMEOUT) {
    isPowerSave = true;
  }
}

void debounceButtons() {
  while(digitalRead(MENU_PIN) == LOW)
    ;
  while(digitalRead(PREV_PIN) == LOW)
    ;
  while(digitalRead(NEXT_PIN) == LOW)
    ;
}

void __log(const char *fmt, ...) {
  if(txDisabled)
    return;
  
  char _log[128];
  va_list arguments;
  va_start(arguments, fmt);
  vsnprintf_P(_log, ArraySize(_log) - 1, fmt, arguments);
  va_end(arguments);
  Serial.print(F("echo: "));
  Serial.println(_log);
}

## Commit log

2021-07-28 Added PCB Rev.2 design
    [SFB-B_Cu.gbr, SFB-B_Mask.gbr, SFB-B_Paste.gbr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]
2022-08-06 Updated; See README.md
    [SFB-BOM.csv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]
2022-08-06 Added link for ordering PCBs
2022-08-07 Added Daisy-Chaining; See README.md
2022-08-08 Reworked Daisy-Chain wiring; See README.md
    [SFB.h, Smart-Filament-Buffer.cpp]

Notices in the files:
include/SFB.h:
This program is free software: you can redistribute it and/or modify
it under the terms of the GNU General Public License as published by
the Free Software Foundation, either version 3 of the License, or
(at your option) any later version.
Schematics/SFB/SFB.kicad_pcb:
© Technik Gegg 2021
